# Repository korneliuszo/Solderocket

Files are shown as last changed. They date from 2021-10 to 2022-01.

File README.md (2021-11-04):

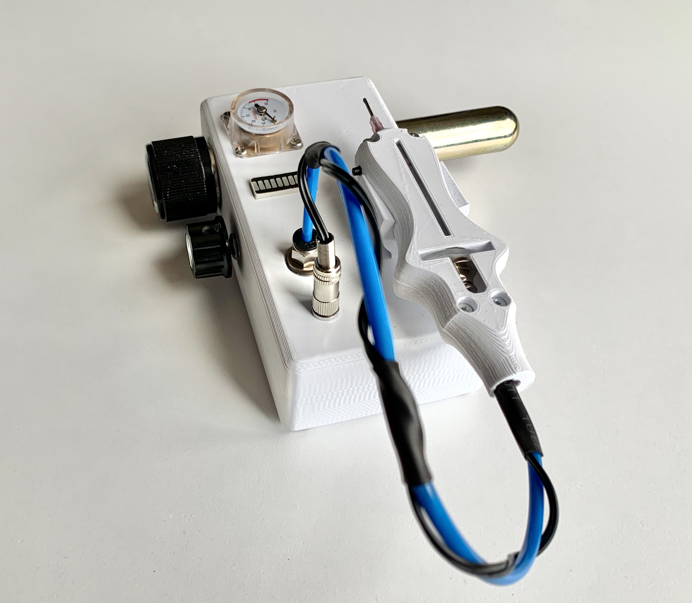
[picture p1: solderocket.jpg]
Solderocket


# Solderocket
Regular solder paste dispensers must be connected to compressed air which you can provide with huge compressor. As a maker I can not run a large compressor in my room because of its noise and footprint.

Stencils might be a solution but for small size PCB work they are too dirty and I don't like to touch the chemical solder paste with my hands and tools. It takes more time to clean up every time than apply it to the PCB.

That's why I decided to design a desktop solder paste dispenser that is clean, easy to use and small in size. I call it Solderocket.

Using the rotary knobs, the time and pressure can be set so that the right dot size can be selected for each type of solder paste.

This device is indispensable when working with SMD on a regular basis. SMD paste can be dosed very accurately and quickly. Adhesives can be used in addition to SMD paste.

# Specifications
* No Compressor needed. Works with Co2 cartridges.
* Adjustable pressure 0-60 psi 
* Adjustable timing from 50 millisecond up to trigger release.
* Ergonomic Injector hand tool
* Dimensions : 155 x 120 x 75 mm
* Weight : 770 gr  (without packaging)
* Works with 12V DC adapter

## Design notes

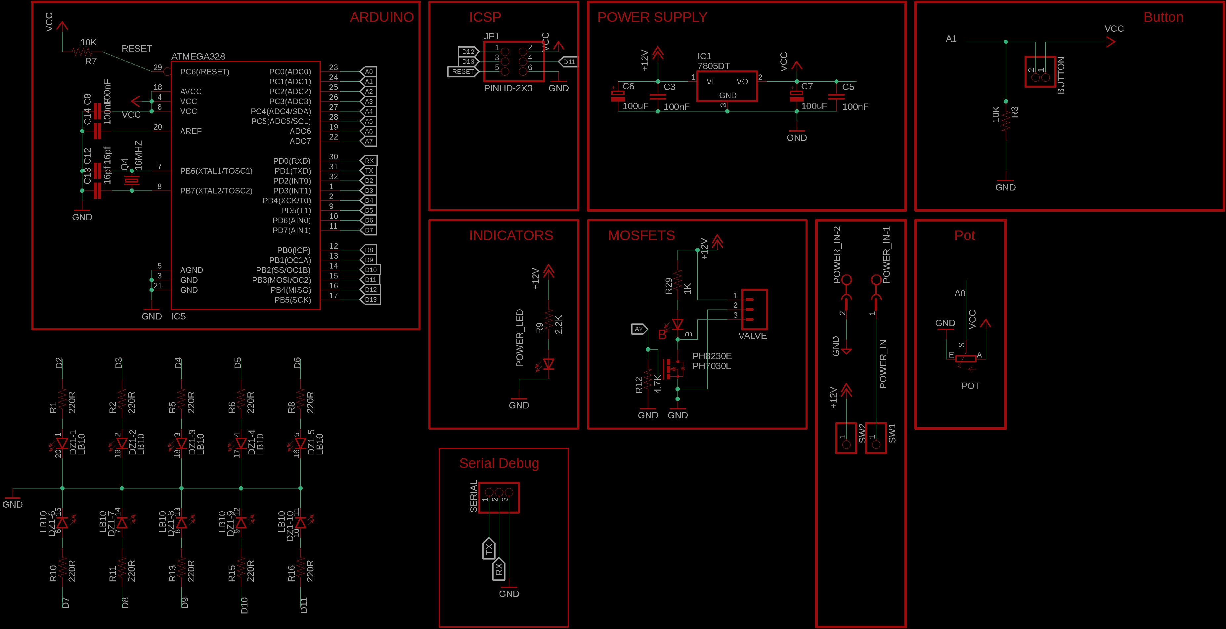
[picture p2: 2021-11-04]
pcb/schematic_img.png

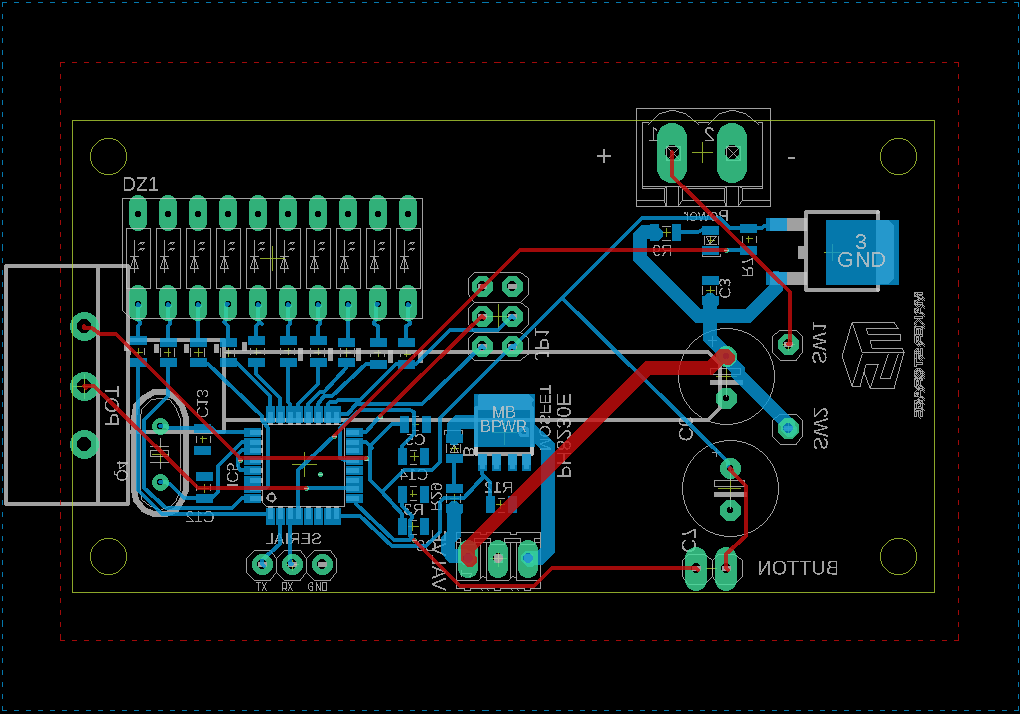
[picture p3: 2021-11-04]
pcb/board_image.png

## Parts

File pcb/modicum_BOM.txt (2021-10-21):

Partlist exported from /home/nuri/electronics/modicum/pcb/modicum.sch at 14.10.2021 13:22

Qty Value     Device             Package    Parts                                       Description                              CATEGORY  DESCRIPTION MANUFACTURER MF MPN OC_FARNELL OC_NEWARK OPERATING_TEMP PART_STATUS POPULARITY ROHS_COMPLIANT SERIES SUB-CATEGORY THERMALLOSS TYPE
2             LED0805            LED-0805   B, POWER_LED                                LEDs                                                                                                                                                                                             
1             M03                03P        VALVE                                       AMP QUICK CONNECTOR                                                                unknown    unknown                              12                                                            
2             PINHD-1X1          1X01       SW1, SW2                                    PIN HEADER                                                                                                                         64                                                            
1             PINHD-1X2          1X02       BUTTON                                      PIN HEADER                                                                                                                         98                                                            
1             PINHD-1X3          1X03       SERIAL                                      PIN HEADER                                                                                                                                                                                       
1             TRIM_EU-CIP20C-6MM CIP20C-6MM POT                                         POTENTIOMETER                                                                                                                                                                                    
4   100nF     CAP0805            0805       C3, C5, C8, C14                             Capacitor                                                                                                                                                                                        
2   100uF     CPOL-EUE3.5-8      E3,5-8     C6, C7                                      POLARIZED CAPACITOR, European symbol                                                                                                                                                             
2   10K       RESISTOR           0805       R3, R7                                      Resistor                                                                                                                                                                                         
1   16MHZ     CRYSTALHC49S       HC49/S     Q4                                          CRYSTAL                                                                                                                                                                                          
2   16pf      CAP0805            0805       C12, C13                                    Capacitor                                                                                                                                                                                        
1   1K        RESISTOR           0805       R29                                         Resistor                                                                                                                                                                                         
1   2.2K      RESISTOR           0805       R9                                          Resistor                                                                                                                                                                                         
10  220R      RESISTOR           0805       R1, R2, R5, R6, R8, R10, R11, R13, R15, R16 Resistor                                                                                                                                                                                         
1   4.7K      RESISTOR           0805       R12                                         Resistor                                                                                                                                                                                         
1   7805DT    7805DT             TO252      IC1                                         Positive VOLTAGE REGULATOR                                                                                                                                                                       
1   ATMEGA328 ATMEGA168          TQFP32-08  IC5                                                                                                                                                                                                                                          
1   LB10      LB10               LB10       DZ1                                         LED BLOCK                                                                                                                          1                                                             
1   MST2V     MST2V              MSTBV2     POWER_IN                                    PHOENIX                                                                                                                                                                                          
1   PH7030L   PH7030L            SOT669     PH8230E                                     N-channel TrenchMOS (TM) logic level FET                                                                                                                                                         
1   PINHD-2X3 PINHD-2X3          2X03       JP1                                         PIN HEADER                               CONNECTOR                                                                                                                  PIN-HEADER

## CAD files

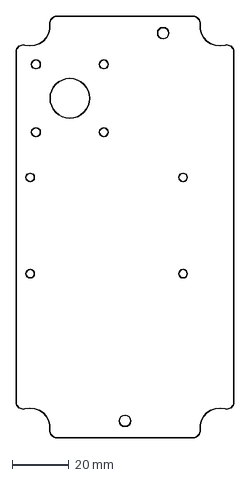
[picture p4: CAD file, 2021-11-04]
2D_Files/sheet_metal.dxf
77.0 x 149.0 mm

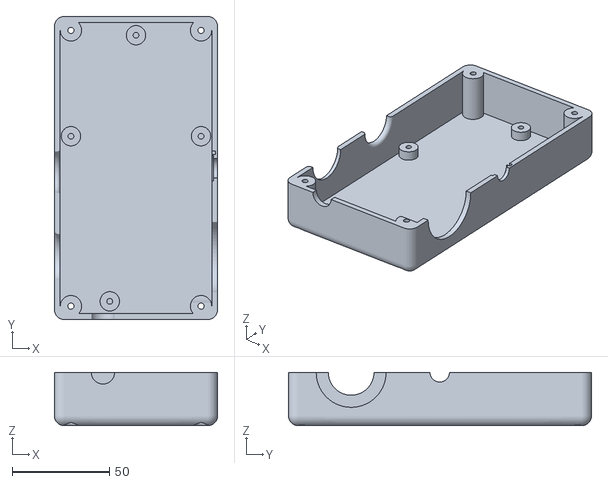
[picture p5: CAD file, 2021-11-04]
3D_files/STL/alt v70.stl
84.0 x 156.0 x 27.4

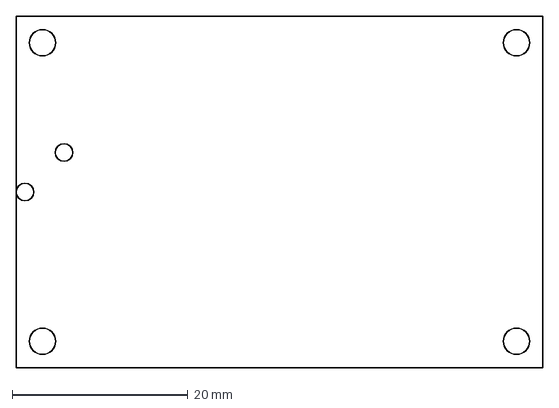
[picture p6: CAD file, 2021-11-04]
2D_Files/pcb.dxf
60.0 x 40.0 mm

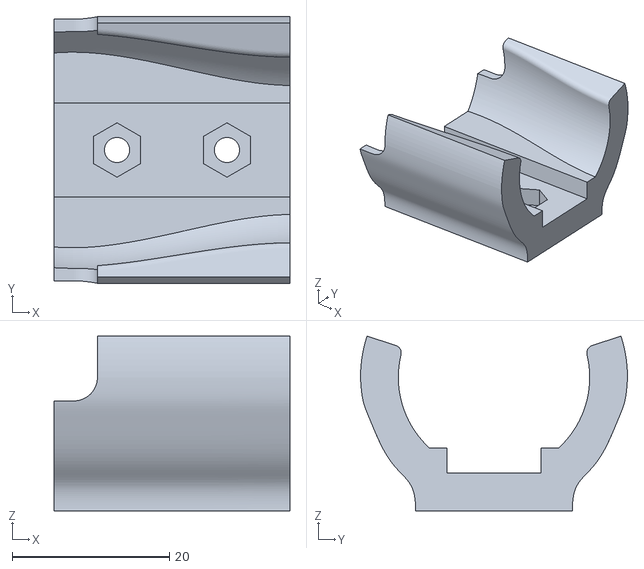
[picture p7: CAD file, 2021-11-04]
3D_files/STL/el_tutac v20.stl
30.0 x 34.0 x 22.3

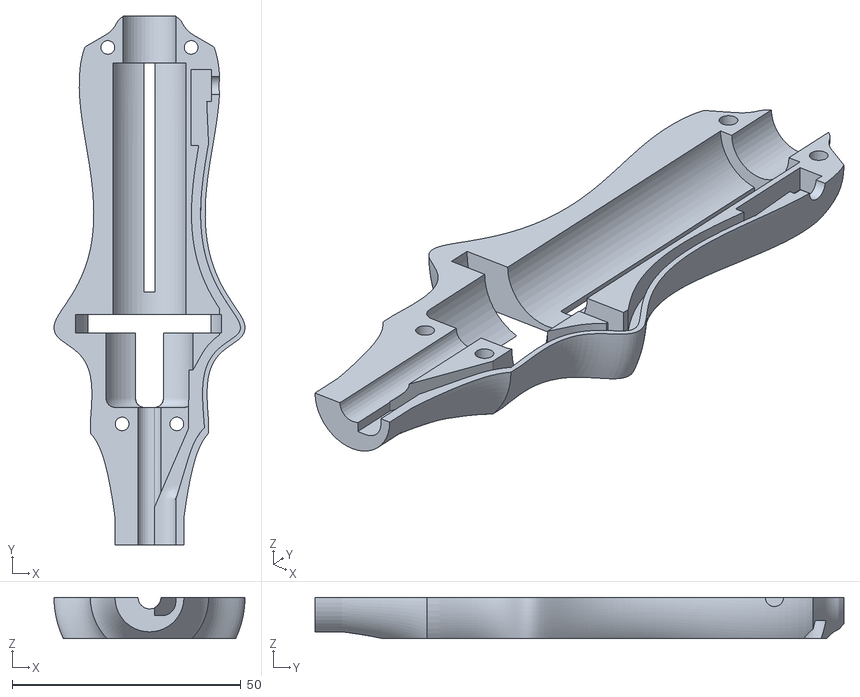
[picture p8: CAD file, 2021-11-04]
3D_files/STL/syringe_holder_alt v55.stl
41.7 x 115.5 x 9.00

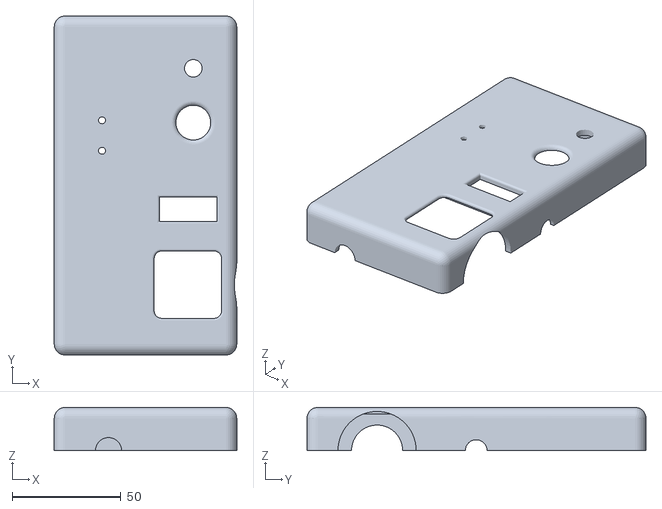
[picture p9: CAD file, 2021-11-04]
3D_files/STL/ust v64.stl
84.0 x 156.0 x 19.9

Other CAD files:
3D_files/STL/syringe_holder_ust v3.stl

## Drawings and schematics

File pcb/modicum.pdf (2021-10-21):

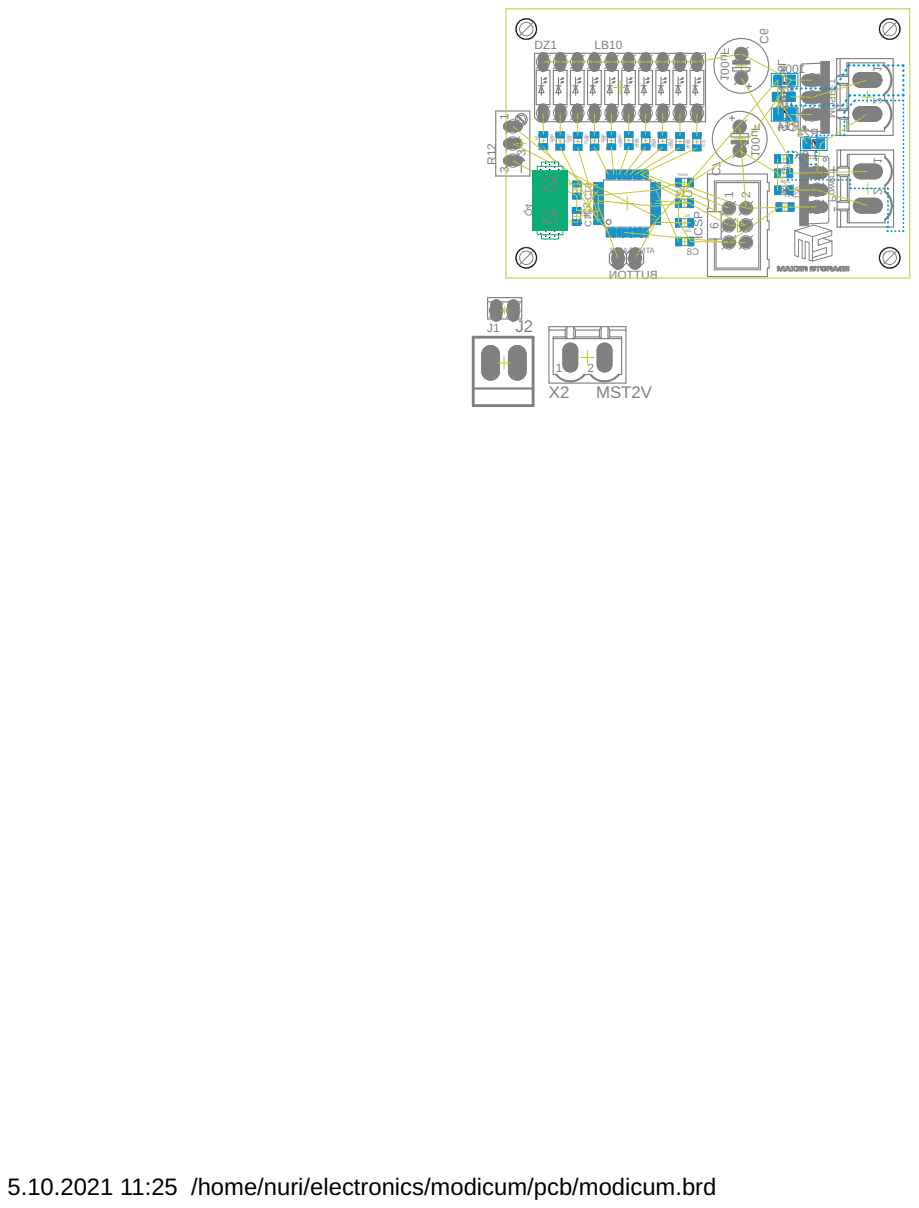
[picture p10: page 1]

5.10.2021 11:25 /home/nuri/electronics/modicum/pcb/modicum.brd

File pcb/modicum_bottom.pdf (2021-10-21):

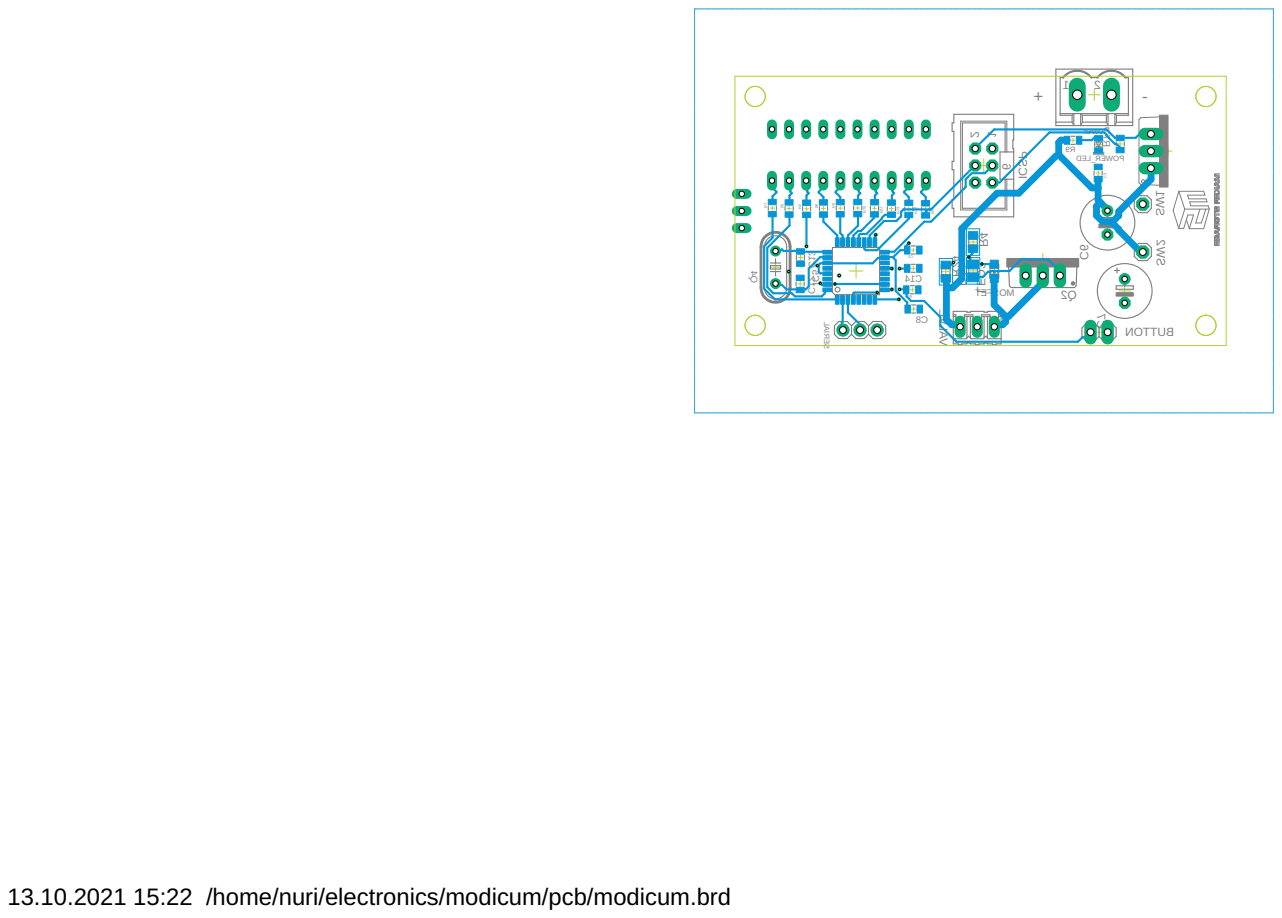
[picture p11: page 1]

13.10.2021 15:22 /home/nuri/electronics/modicum/pcb/modicum.brd

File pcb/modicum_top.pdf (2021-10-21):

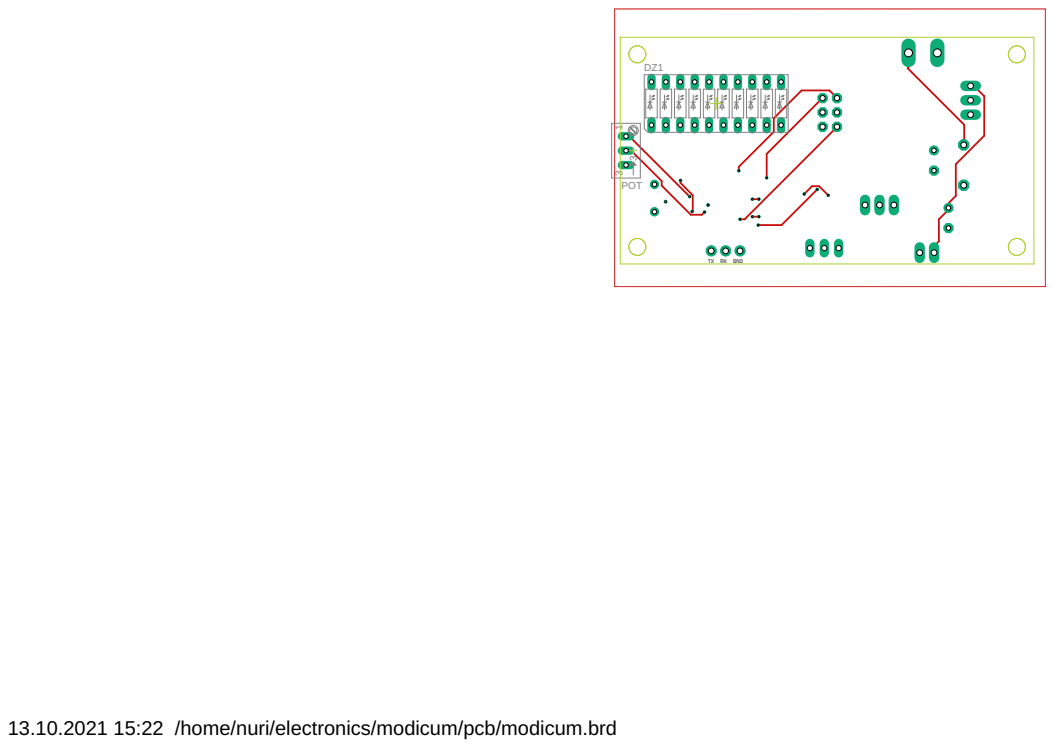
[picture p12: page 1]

13.10.2021 15:22 /home/nuri/electronics/modicum/pcb/modicum.brd

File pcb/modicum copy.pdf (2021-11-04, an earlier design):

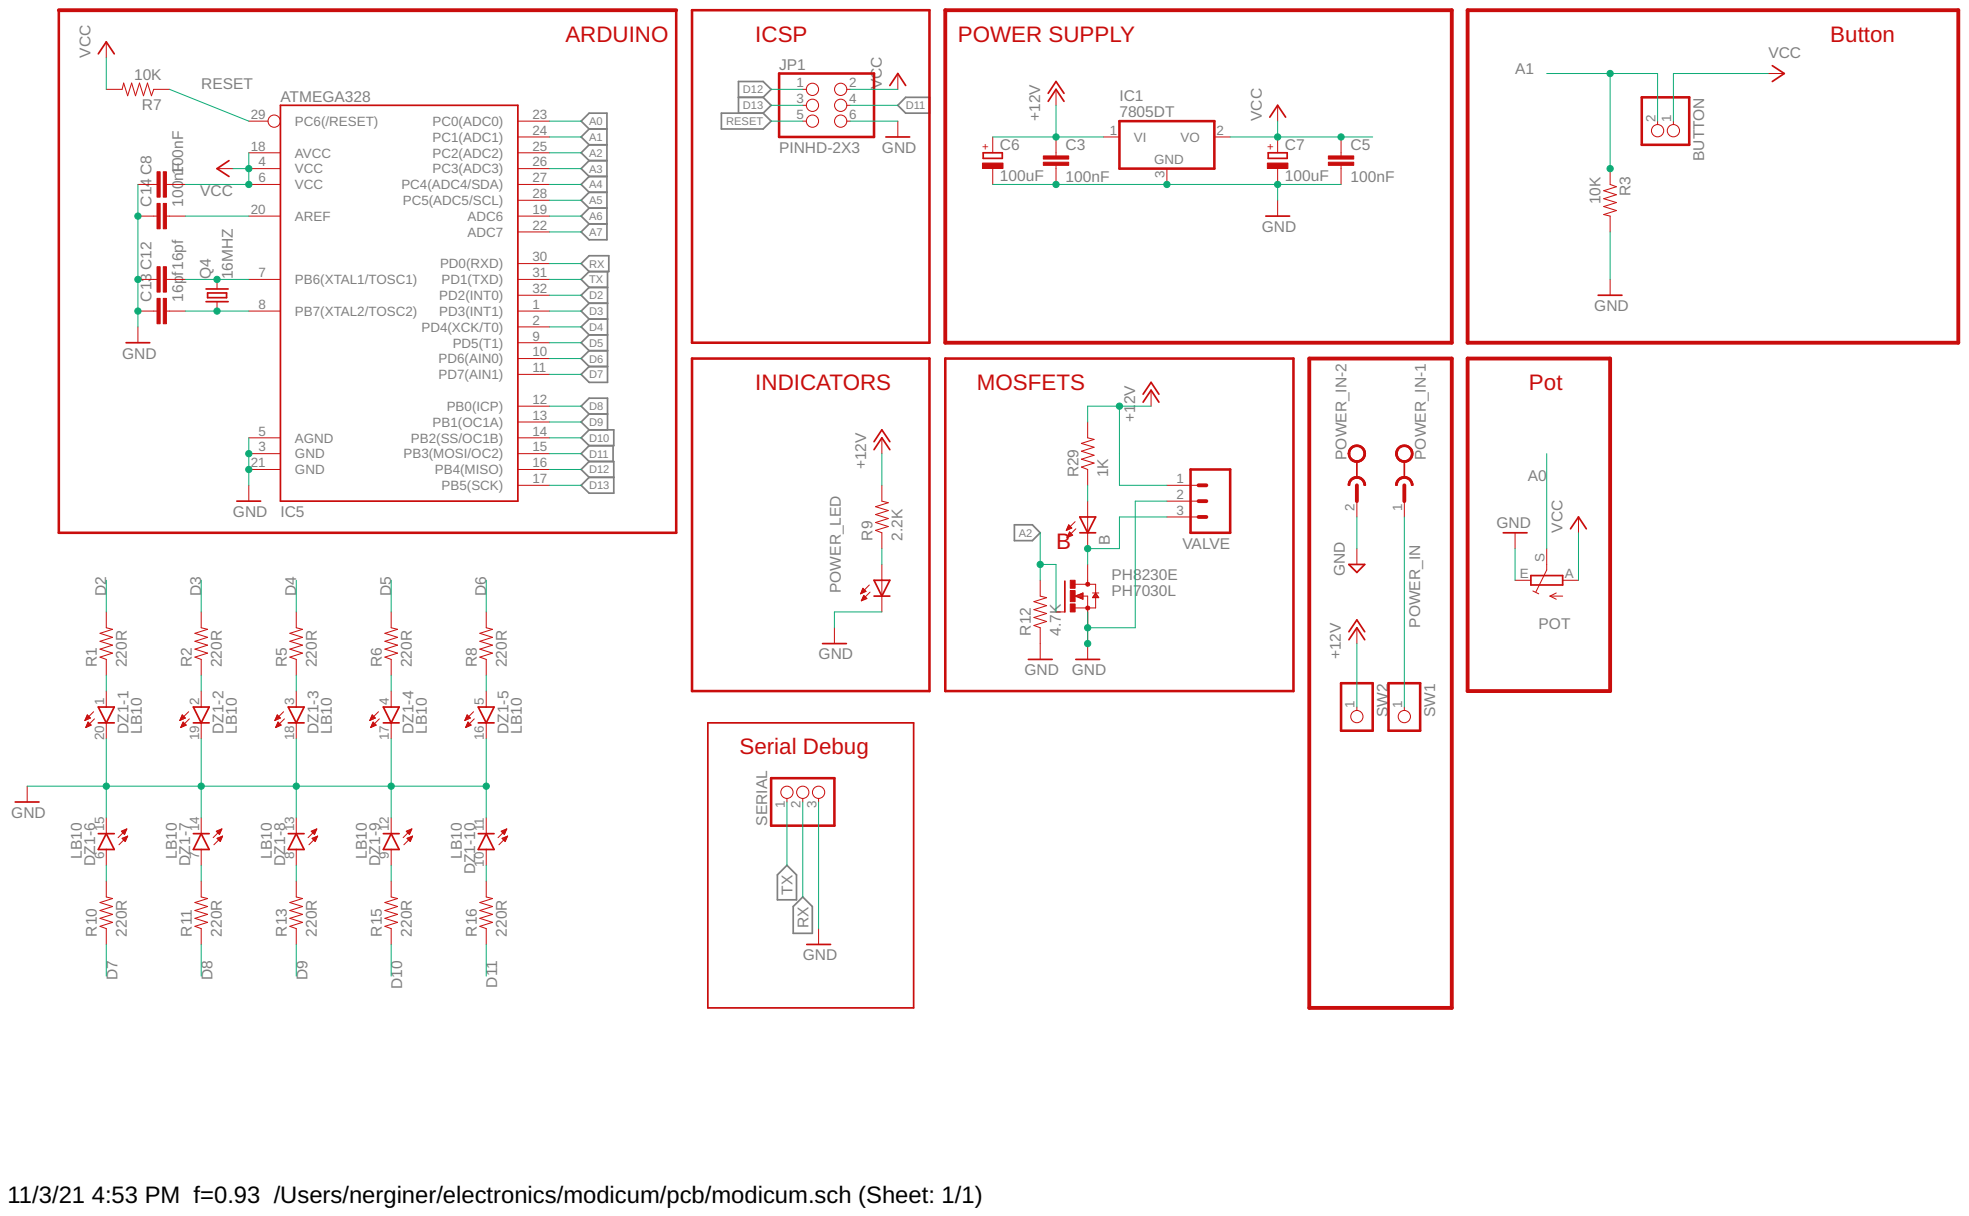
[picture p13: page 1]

11/3/21 4:53 PM f=0.93 /Users/nerginer/electronics/modicum/pcb/modicum.sch (Sheet: 1/1)

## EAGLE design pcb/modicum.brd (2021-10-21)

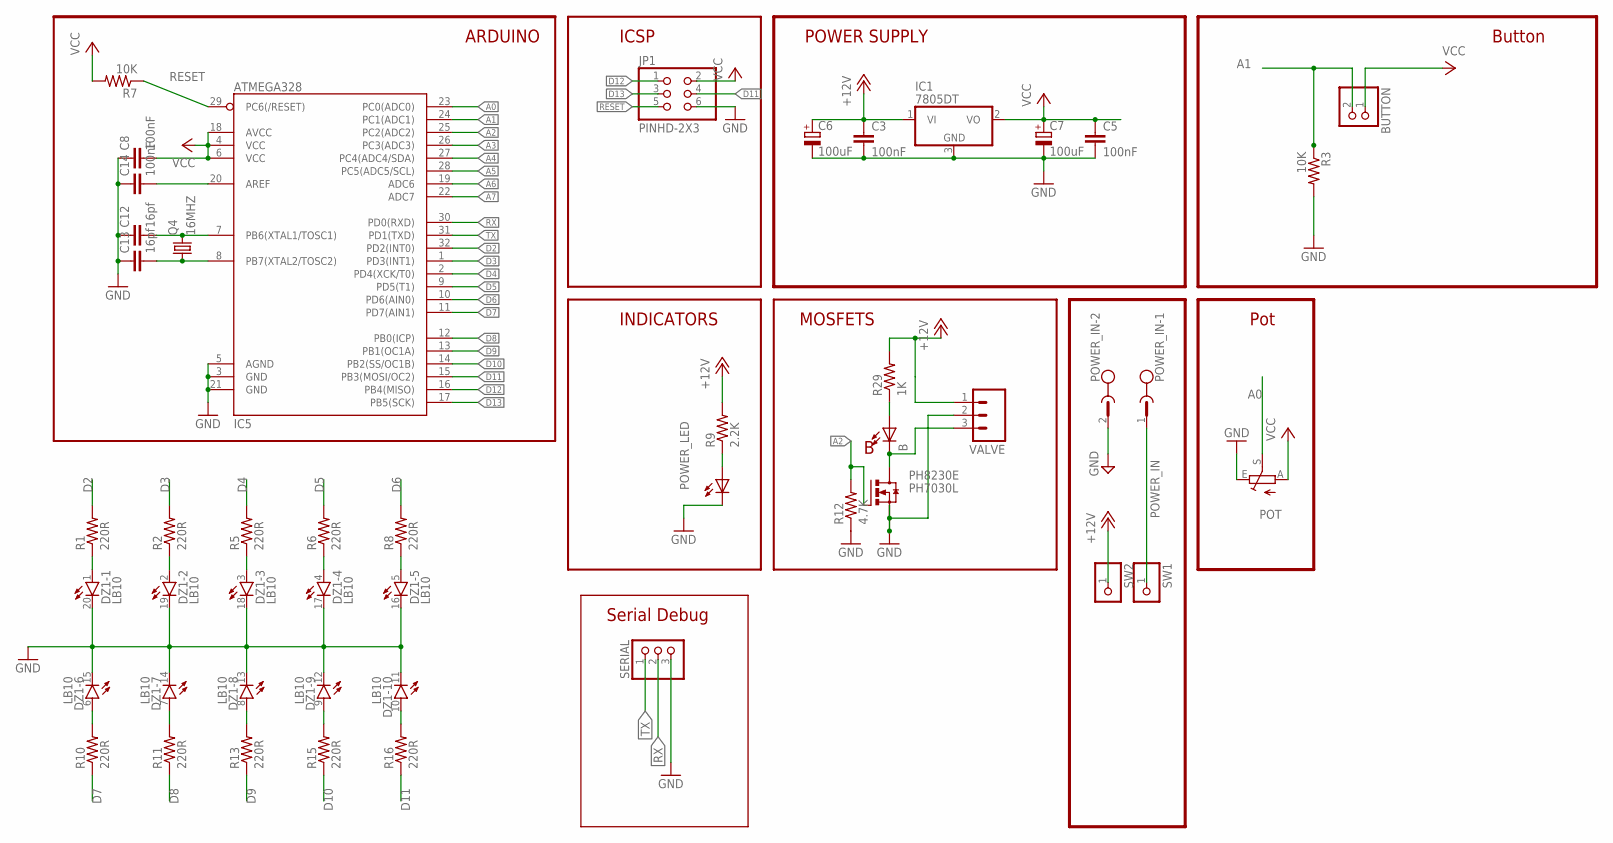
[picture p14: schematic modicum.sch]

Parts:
B: LED0805; LED-0805
BUTTON: PINHD-1X2; 1X02
C3, C5, C8, C14: 100nF; 0805
C6, C7: 100uF; E3,5-8
C12, C13: 16pf; 0805
DZ1: LB10
IC1: 7805DT; TO252
IC5: ATMEGA328; TQFP32-08
JP1: PINHD-2X3; 2X03
PH8230E: PH7030L; SOT669
POT: TRIM_EU-CIP20C-6MM; CIP20C-6MM
POWER_IN: MST2V; MSTBV2
POWER_LED: LED0805; LED-0805
Q4: 16MHZ; HC49/S
R1, R2, R5, R6, R8, R10, R11, R13, R15, R16: 220R; 0805
R3, R7: 10K; 0805
R9: 2.2K; 0805
R12: 4.7K; 0805
R29: 1K; 0805
SERIAL: PINHD-1X3; 1X03
SW1, SW2: PINHD-1X1; 1X01
VALVE: M03; 03P

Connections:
+12V: C3.1, C6.+, IC1.1 (VI), R9.2, R29.2, SW2.1, VALVE.1
A0: IC5.23 (PC0(ADC0)), POT.S
A1: BUTTON.2, IC5.24 (PC1(ADC1)), R3.1
A2: IC5.25 (PC2(ADC2)), PH8230E.4 (G), R12.2
A3: IC5.26 (PC3(ADC3))
A4: IC5.27 (PC4(ADC4/SDA))
A5: IC5.28 (PC5(ADC5/SCL))
A6: IC5.19 (ADC6)
A7: IC5.22 (ADC7)
BPWR: B.C, PH8230E.MB (D), VALVE.3
D2: IC5.32 (PD2(INT0)), R1.2
D3: IC5.1 (PD3(INT1)), R2.2
D4: IC5.2 (PD4(XCK/T0)), R5.2
D5: IC5.9 (PD5(T1)), R6.2
D6: IC5.10 (PD6(AIN0)), R8.2
D7: IC5.11 (PD7(AIN1)), R10.1
D8: IC5.12 (PB0(ICP)), R11.1
D9: IC5.13 (PB1(OC1A)), R13.1
D10: IC5.14 (PB2(SS/OC1B)), R15.1
D11: IC5.15 (PB3(MOSI/OC2)), JP1.4, R16.1
D12: IC5.16 (PB4(MISO)), JP1.1
D13: IC5.17 (PB5(SCK)), JP1.3
GND: C3.2, C5.2, C6.-, C7.-, C8.1, C12.1, C13.1, C14.1, DZ1.11 (C), DZ1.12 (C), DZ1.13 (C), DZ1.14 (C), DZ1.15 (C), DZ1.16 (C), DZ1.17 (C), DZ1.18 (C), DZ1.19 (C), DZ1.20 (C), IC1.3 (GND), IC5.3 (GND), IC5.5 (AGND), IC5.21 (GND), JP1.6, PH8230E.1 (S), PH8230E.2 (S), PH8230E.3 (S), POT.E, POWER_IN.2, POWER_LED.C, R3.2, R12.1, SERIAL.3, VALVE.2
unnamed: DZ1.1 (A), R1.1
unnamed: DZ1.2 (A), R2.1
unnamed: DZ1.3 (A), R5.1
unnamed: DZ1.4 (A), R6.1
unnamed: DZ1.5 (A), R8.1
unnamed: DZ1.6 (A), R10.2
unnamed: DZ1.7 (A), R11.2
unnamed: DZ1.8 (A), R13.2
unnamed: DZ1.9 (A), R15.2
unnamed: DZ1.10 (A), R16.2
unnamed: C14.2, IC5.20 (AREF)
unnamed: POWER_LED.A, R9.1
unnamed: C12.2, IC5.7 (PB6(XTAL1/TOSC1)), Q4.2
unnamed: C13.2, IC5.8 (PB7(XTAL2/TOSC2)), Q4.1
unnamed: B.A, R29.1
POWER_IN: POWER_IN.1, SW1.1
RESET: IC5.29 (PC6(/RESET)), JP1.5, R7.1
RX: IC5.30 (PD0(RXD)), SERIAL.2
TX: IC5.31 (PD1(TXD)), SERIAL.1
VCC: BUTTON.1, C5.1, C7.+, C8.2, IC1.2 (VO), IC5.4 (VCC), IC5.6 (VCC), IC5.18 (AVCC), JP1.2, POT.A, R7.2

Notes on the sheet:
MOSFETS
ICSP
ARDUINO
INDICATORS
POWER SUPPLY
Button
Pot
Serial Debug

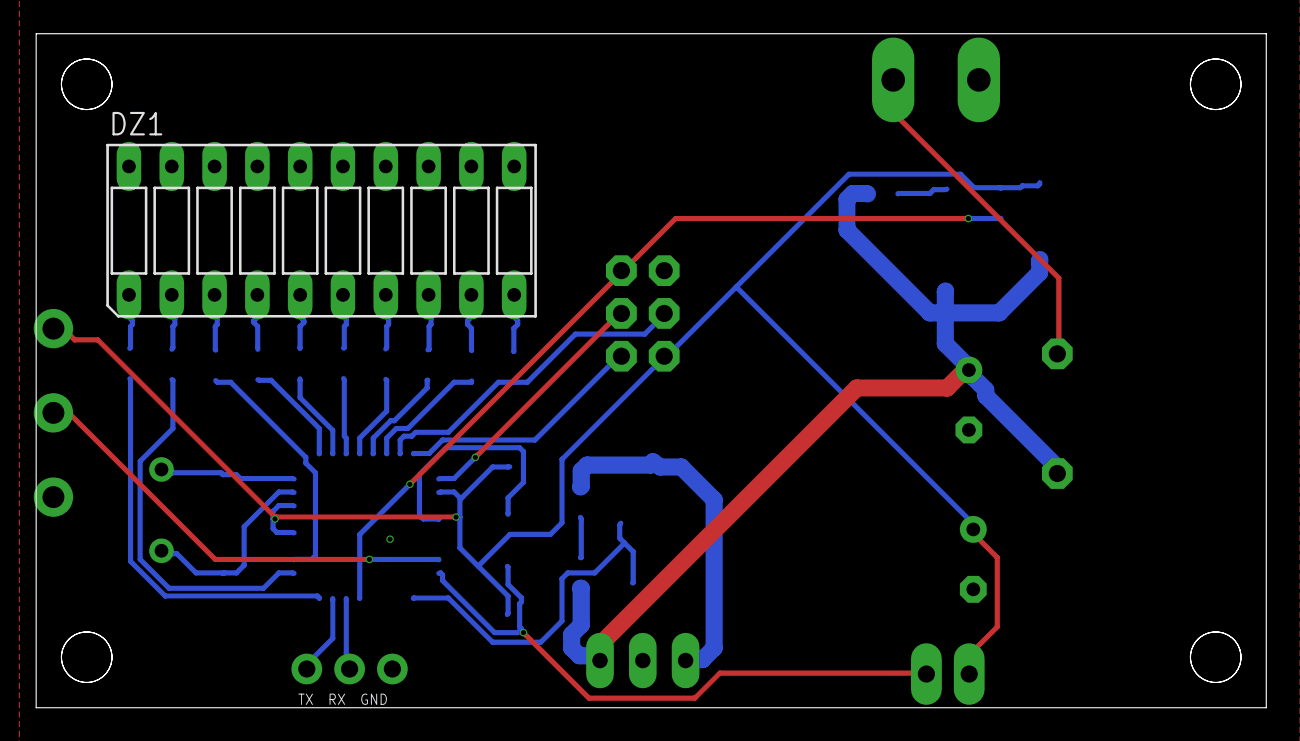
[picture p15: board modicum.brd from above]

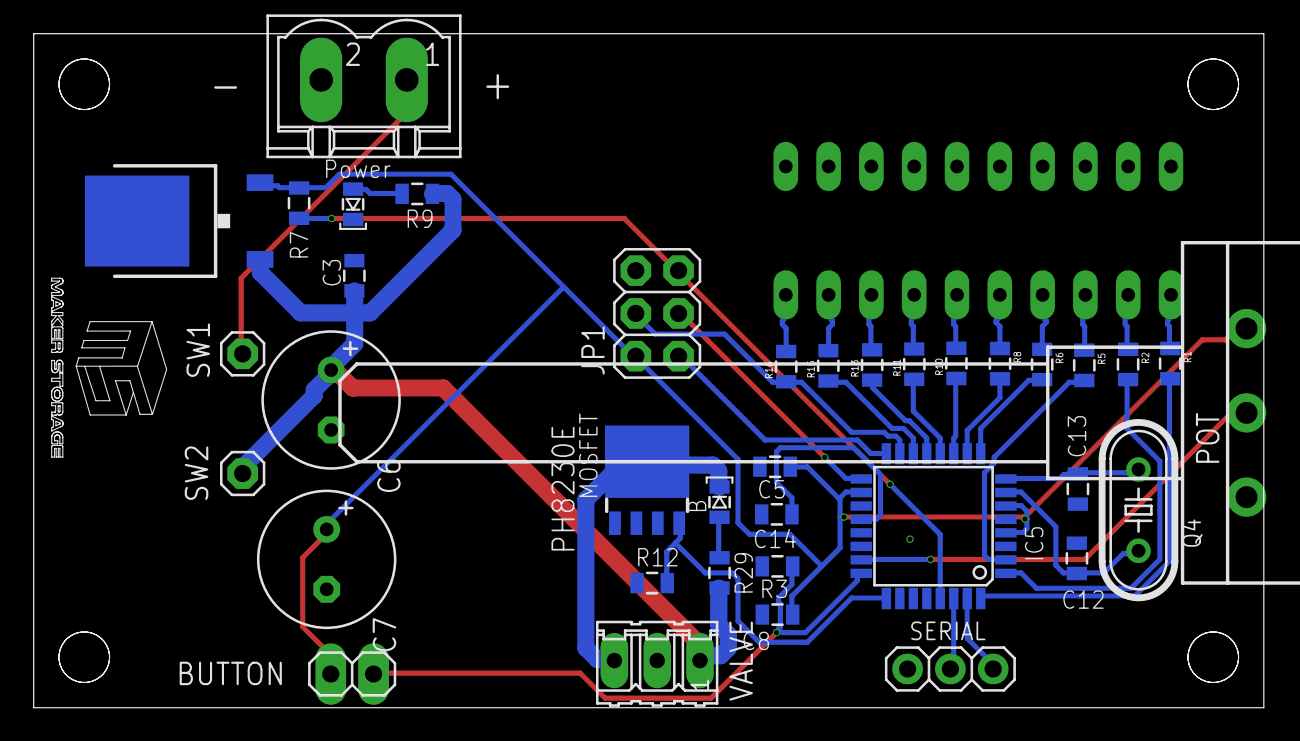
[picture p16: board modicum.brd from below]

Board: 2 copper layers, 73.0 x 40.0 mm, 38 parts (37 on the bottom side), 38 nets.

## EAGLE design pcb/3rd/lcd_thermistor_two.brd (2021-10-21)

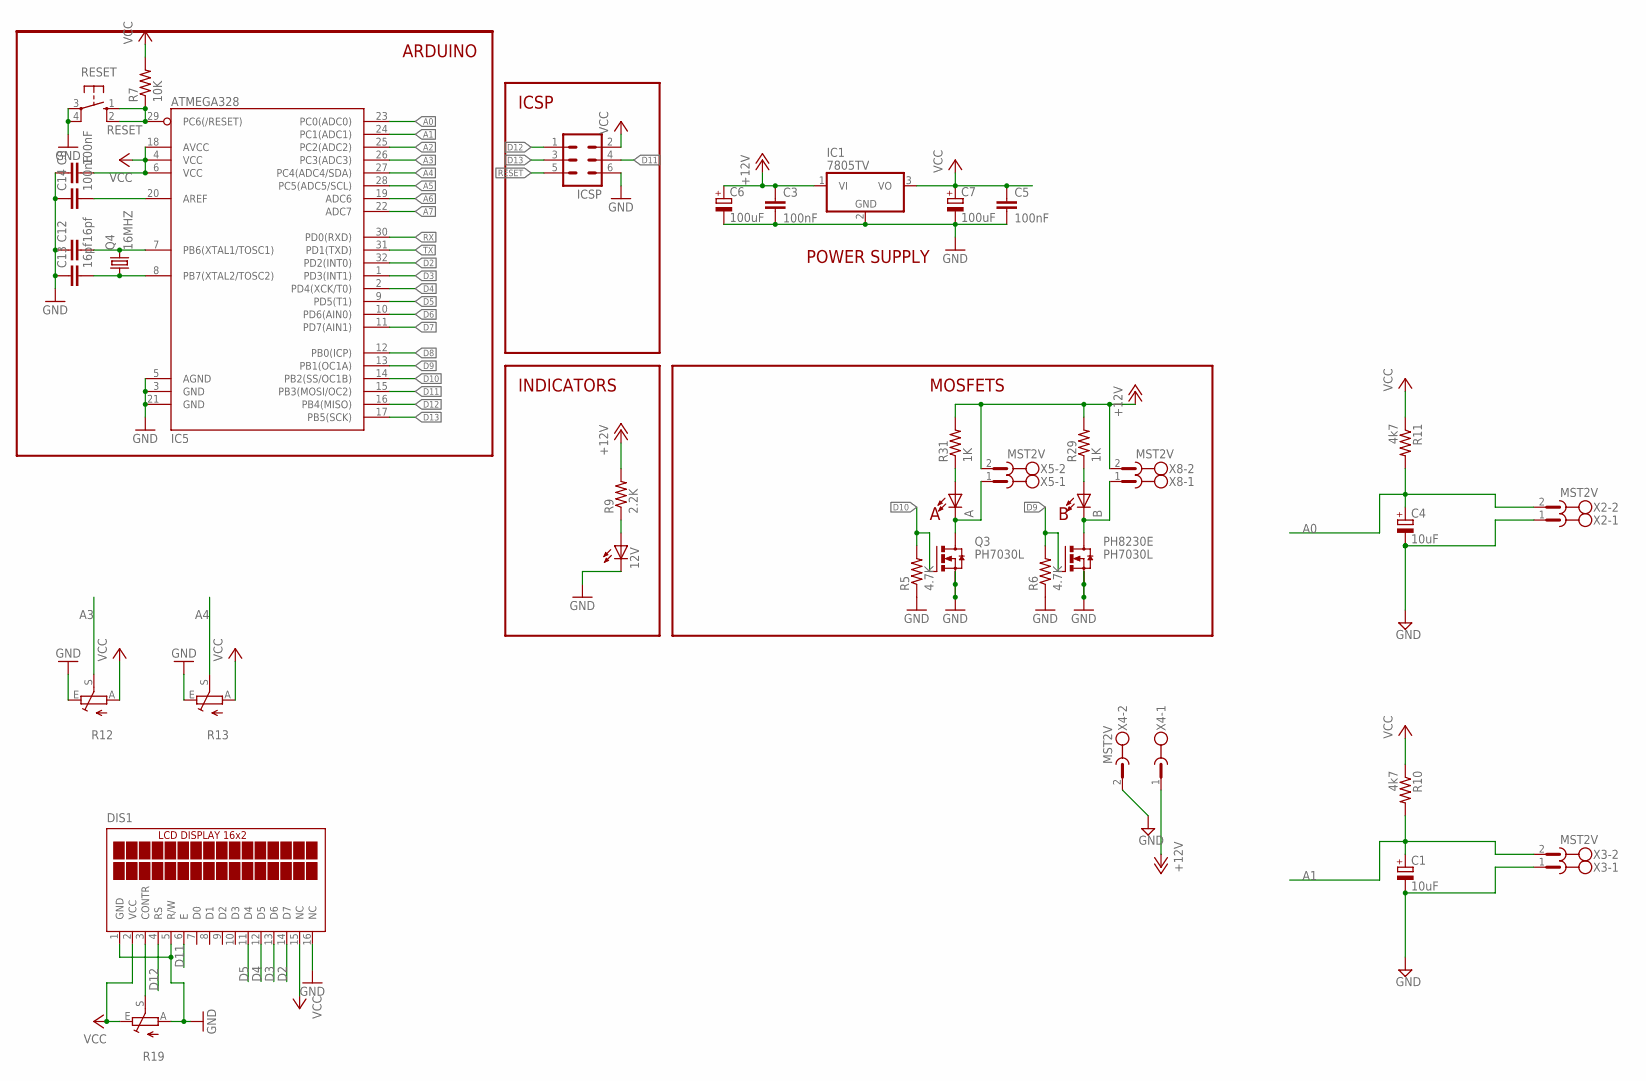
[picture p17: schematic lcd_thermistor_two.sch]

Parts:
12V: LED0805; LED-0805
A: LED0805; LED-0805
B: LED0805; LED-0805
C1, C4: 10uF; E5-6
C3, C5, C8, C14: 100nF; 0805
C6, C7: 100uF; E3,5-8
C12, C13: 16pf; 0805
DIS1: TUXGR_16X2_R2
IC1: 7805TV; TO220V
IC5: ATMEGA328; TQFP32-08
ICSP: ML6
PH8230E: PH7030L; SOT669
Q3: PH7030L; SOT669
Q4: 16MHZ; HC49/S
R5, R6: 4.7K; 0805
R7: 10K; 0805
R9: 2.2K; 0805
R10, R11: 4k7; 0805
R12, R13: TRIM_EU-B25U; B25U
R19: TRIM_EU-B25P; B25P
R29, R31: 1K; 0805
RESET: 10-XX; B3F-10XX
X2, X3, X4, X5, X8: MST2V; MSTBV2

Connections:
+12V: C3.1, C6.+, IC1.1 (VI), R9.2, R29.2, R31.2, X4.1, X5.2, X8.2
A0: C4.+, IC5.23 (PC0(ADC0)), R11.2, X2.2
A1: C1.+, IC5.24 (PC1(ADC1)), R10.2, X3.2
A2: IC5.25 (PC2(ADC2))
A3: IC5.26 (PC3(ADC3)), R12.S
A4: IC5.27 (PC4(ADC4/SDA)), R13.S
A5: IC5.28 (PC5(ADC5/SCL))
A6: IC5.19 (ADC6)
A7: IC5.22 (ADC7)
APWR: A.C, Q3.MB (D), X5.1
BPWR: B.C, PH8230E.MB (D), X8.1
D2: DIS1.14 (D7), IC5.32 (PD2(INT0))
D3: DIS1.13 (D6), IC5.1 (PD3(INT1))
D4: DIS1.12 (D5), IC5.2 (PD4(XCK/T0))
D5: DIS1.11 (D4), IC5.9 (PD5(T1))
D6: IC5.10 (PD6(AIN0))
D7: IC5.11 (PD7(AIN1))
D8: IC5.12 (PB0(ICP))
D9: IC5.13 (PB1(OC1A)), PH8230E.4 (G), R6.2
D10: IC5.14 (PB2(SS/OC1B)), Q3.4 (G), R5.2
D11: DIS1.6 (E), IC5.15 (PB3(MOSI/OC2)), ICSP.4
D12: DIS1.4 (RS), IC5.16 (PB4(MISO)), ICSP.1
D13: IC5.17 (PB5(SCK)), ICSP.3
GND: 12V.C, C1.-, C3.2, C4.-, C5.2, C6.-, C7.-, C8.1, C12.1, C13.1, C14.1, DIS1.1 (GND), DIS1.5 (R/W), DIS1.16 (NC), IC1.2 (GND), IC5.3 (GND), IC5.5 (AGND), IC5.21 (GND), ICSP.6, PH8230E.1 (S), PH8230E.2 (S), PH8230E.3 (S), Q3.1 (S), Q3.2 (S), Q3.3 (S), R5.1, R6.1, R12.E, R13.E, R19.A, RESET.3, RESET.4 (P1), X2.1, X3.1, X4.2
unnamed: C14.2, IC5.20 (AREF)
unnamed: 12V.A, R9.1
unnamed: DIS1.3 (CONTR), R19.S
unnamed: C12.2, IC5.7 (PB6(XTAL1/TOSC1)), Q4.2
unnamed: C13.2, IC5.8 (PB7(XTAL2/TOSC2)), Q4.1
unnamed: A.A, R31.1
unnamed: B.A, R29.1
RESET: IC5.29 (PC6(/RESET)), ICSP.5, R7.1, RESET.1 (S), RESET.2 (S1)
RX: IC5.30 (PD0(RXD))
TX: IC5.31 (PD1(TXD))
VCC: C5.1, C7.+, C8.2, DIS1.2 (VCC), DIS1.15 (NC), IC1.3 (VO), IC5.4 (VCC), IC5.6 (VCC), IC5.18 (AVCC), ICSP.2, R7.2, R10.1, R11.1, R12.A, R13.A, R19.E

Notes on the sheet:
MOSFETS
ICSP
ARDUINO
INDICATORS
POWER SUPPLY

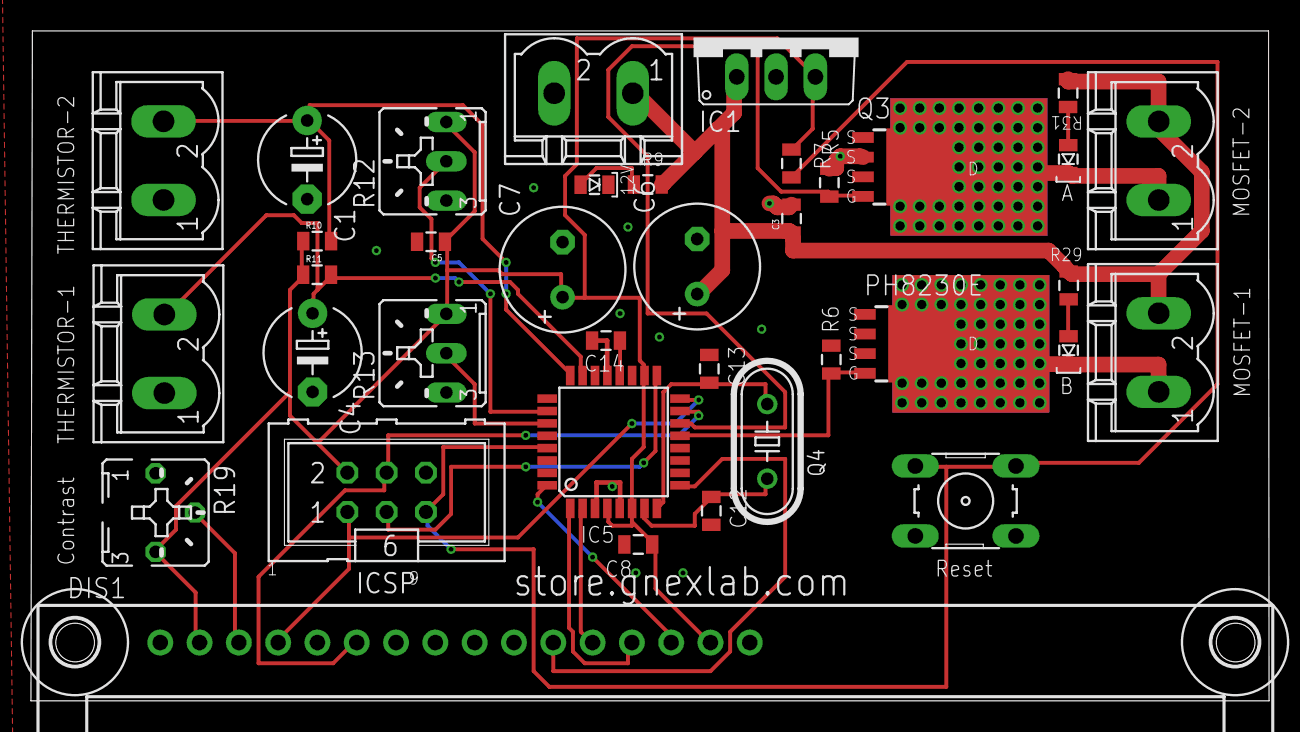
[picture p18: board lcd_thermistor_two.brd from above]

Board: 2 copper layers, 80.0 x 43.3 mm, 39 parts (0 on the bottom side), 26 nets.

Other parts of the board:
U$1, U$4: 3,0

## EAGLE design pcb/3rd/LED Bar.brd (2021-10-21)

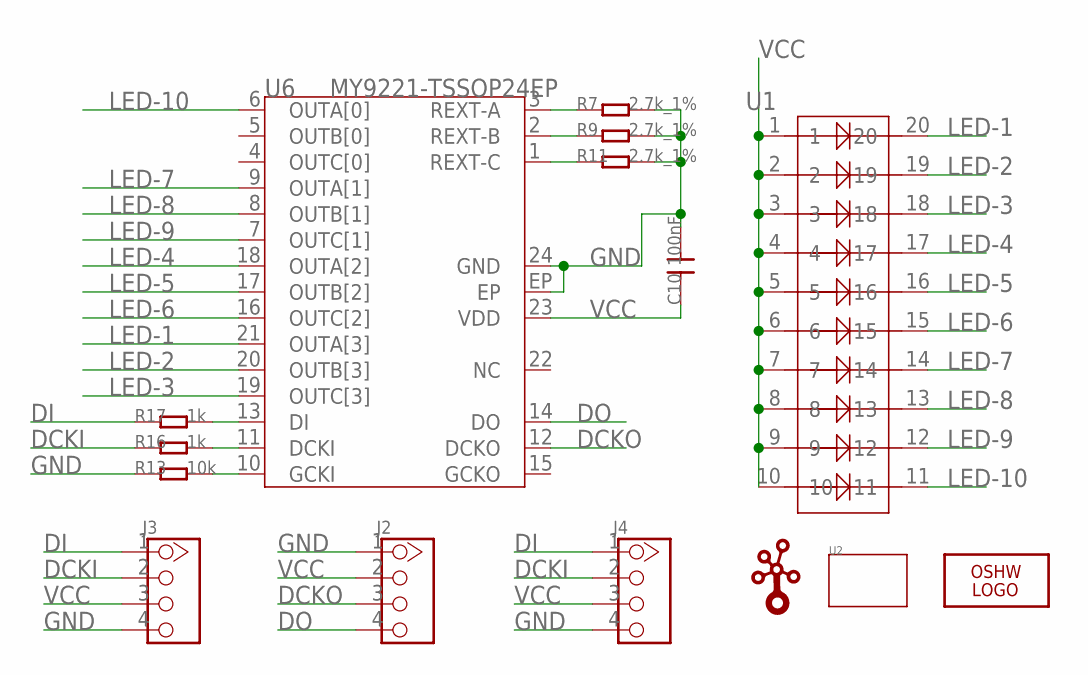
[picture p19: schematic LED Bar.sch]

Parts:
C10: 100nF; 0603
J2: HEADER-4P-90D; 4P-2.54-90
J3: HEADER-4P'2.54-90D-FEMALE'; 4P-2.54-90D-FEMALE
J4: TWIG-4P-2.0-2.0; 4P-2.0
LOGO1: LOGO-OSHW-FILLX0150-NT; OSHW_FILLX150_NOTEXT
R7, R9, R11: 2.7k_1%; 0603
R13: 10k; 0603
R16, R17: 1k; 0603
U1: LED-20P; 20P-DIP-2.54-25.5X10.1X8.4H
U2: TWIG-2U; 2U-DIM-W/-DRILL
U6: MY9221-TSSOP24EP; TSSOP24EP
U$1: LOGO-TWIGTWIGLOGO_SMALL; TWIGLOGO_SMALL

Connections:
DCKI: J3.2, J4.2, R16.1
DCKO: J2.3, U6.12 (DCKO)
DI: J3.1, J4.1, R17.1
DO: J2.4, U6.14 (DO)
GND: C10.2, J2.1, J3.4, J4.4, R7.2, R9.2, R11.2, R13.1, U6.24 (GND), U6.EP
LED-1: U1.20, U6.21 (OUTA[3])
LED-2: U1.19, U6.20 (OUTB[3])
LED-3: U1.18, U6.19 (OUTC[3])
LED-4: U1.17, U6.18 (OUTA[2])
LED-5: U1.16, U6.17 (OUTB[2])
LED-6: U1.15, U6.16 (OUTC[2])
LED-7: U1.14, U6.9 (OUTA[1])
LED-8: U1.13, U6.8 (OUTB[1])
LED-9: U1.12, U6.7 (OUTC[1])
LED-10: U1.11, U6.6 (OUTA[0])
unnamed: R17.2, U6.13 (DI)
unnamed: R16.2, U6.11 (DCKI)
unnamed: R13.2, U6.10 (GCKI)
unnamed: R11.1, U6.1 (REXT-C)
unnamed: R9.1, U6.2 (REXT-B)
unnamed: R7.1, U6.3 (REXT-A)
VCC: C10.1, J2.2, J3.3, J4.3, U1.1, U1.2, U1.3, U1.4, U1.5, U1.6, U1.7, U1.8, U1.9, U1.10, U6.23 (VDD)

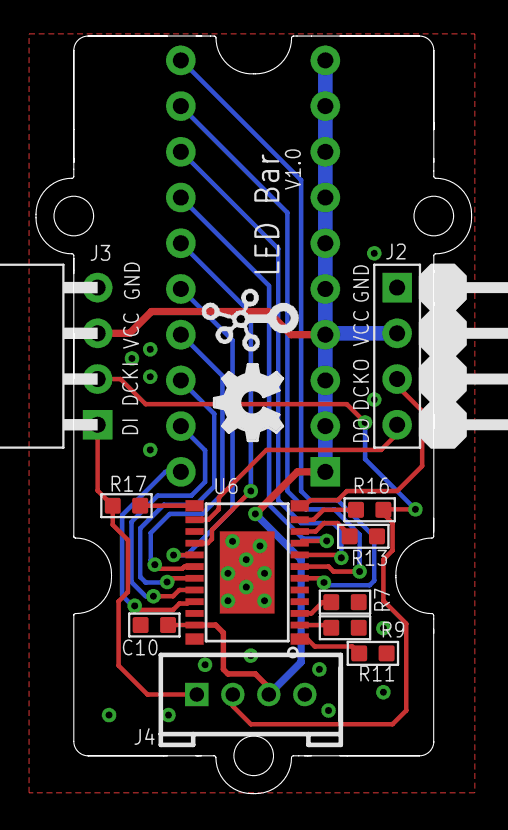
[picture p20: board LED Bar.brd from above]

Board: 2 copper layers, 24.2 x 42.1 mm, 15 parts (1 on the bottom side), 22 nets.

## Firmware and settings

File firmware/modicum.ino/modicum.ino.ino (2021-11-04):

int buttonPin = 15;
int potPin = 0;
int mosfetPin = 16;
int potVal = 0;

const int numReadings = 10;
int readings[numReadings];      // the readings from the analog input
int readIndex = 0;              // the index of the current reading
int total = 0;                  // the running total
int average = 0;                // the average

int buttonState = 1;         // current state of the button, HIGH as we have active low with INPUT_PULLUP
int lastButtonState = 1;     // previous state of the button

const int ledCount = 10;    // the number of LEDs in the bar graph
int ledPins[] = {
  2, 3, 4, 5, 6, 7, 8, 9, 10, 11
};   

void setup() {
  
  // loop over the pin array and set them all to output:
  for (int thisLed = 0; thisLed < ledCount; thisLed++) {
    pinMode(ledPins[thisLed], OUTPUT);
  }
  
  pinMode(mosfetPin, OUTPUT);  
  pinMode(buttonPin, INPUT);    
  pinMode(potPin, INPUT);  

  pinMode(2, OUTPUT); // Do not know why it did not set in the above for loop

}

void loop() {

  buttonState = digitalRead(buttonPin);
    // compare the buttonState to its previous state
    if (buttonState != lastButtonState) {
  
      if (buttonState == LOW) {  
        // wend from off to on:
          digitalWrite(mosfetPin, LOW);
       
      } else {
        // if the current state is LOW then the button
        // wend from on to off:

        digitalWrite(mosfetPin, HIGH); // sets the digital pin 13 on
        delay(average);            // waits for a second
        // if in full throtle do not make it of
        if (average < 999) {
          digitalWrite(mosfetPin, LOW);
        }
          
       
      }
      // Delay a little bit to avoid bouncing
      delay(50);
    }
    // save the current state as the last state,
    //for next time through the loop
    lastButtonState = buttonState;

  average = readPot();

  showLeds(average,50,1000);
 
}

int readPot() {
  
  return map(analogRead(potPin), 0, 1023, 50, 1000);
  
}

void showLeds(int avarage,int mymin,int mymax){

  int ledLevel = map(avarage, mymin, mymax, 0, ledCount);

  // loop over the LED array:
  for (int thisLed = 0; thisLed < ledCount; thisLed++) {
    // if the array element's index is less than ledLevel,
    // turn the pin for this element on:
    if (thisLed < ledLevel) {
      digitalWrite(ledPins[thisLed], HIGH);
    }
    // turn off all pins higher than the ledLevel:
    else {
      digitalWrite(ledPins[thisLed], LOW);
    }
  }
  
}

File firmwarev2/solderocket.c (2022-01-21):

#include <stdint.h>
#include <avr/io.h>
#include <util/delay.h>

static void InitADC(void)
{
 // Select Vref=AVcc
 ADMUX = (1<<REFS0);
 //set prescaller to 128 and enable ADC 
 ADCSRA |= (1<<ADPS2)|(1<<ADPS1)|(1<<ADPS0)|(1<<ADEN);    
}

uint16_t ReadADC(uint8_t ADCchannel)
{
 //select ADC channel with safety mask
 ADMUX = (ADMUX & 0xF0) | (ADCchannel & 0x0F);
 //single conversion mode
 ADCSRA |= (1<<ADSC);
 // wait until ADC conversion is complete
 while( ADCSRA & (1<<ADSC) );
 return ADC;
}

struct {
	volatile uint8_t * port;
	uint8_t mask;
} LEDS[10] =
{
	{&PORTD,0x04},
	{&PORTD,0x08},
	{&PORTD,0x10},
	{&PORTD,0x20},
	{&PORTD,0x40},
	{&PORTD,0x80},
	{&PORTB,0x01},
	{&PORTB,0x02},
	{&PORTB,0x04},
	{&PORTB,0x08},
};

typedef struct {
	uint16_t delay;
	uint16_t led;
} Delays;

//[ round(50*math.exp(x)) for x in [math.log(1000/50)*x/18 for x in range(19)]]

Delays delays[]=
{
	{  50, 0b0000000001},
	{  59, 0b0000000011},
	{  70, 0b0000000010},
	{  82, 0b0000000110},
	{  97, 0b0000000100},
	{ 115, 0b0000001100},
	{ 136, 0b0000001000},
	{ 160, 0b0000011000},
	{ 189, 0b0000010000},
	{ 224, 0b0000110000},
	{ 264, 0b0000100000},
	{ 312, 0b0001100000},
	{ 368, 0b0001000000},
	{ 435, 0b0011000000},
	{ 514, 0b0010000000},
	{ 607, 0b0110000000},
	{ 717, 0b0100000000},
	{ 847, 0b1100000000},
	{1000, 0b1000000000},
};

#define DELAYS_LEN 19

int main(void)
{
	InitADC();
	DDRC=0x04;
	PORTC=0x00;
	DDRD=0xFF;
	PORTD=0x00;
	DDRB=0xFF;
	PORTB=0x00;
	DIDR0=0x01;
	uint8_t lastbutton = 0;	
	while(1)
	{
		uint8_t setting;
		setting = ReadADC(0)/((uint16_t)(1024.0/(DELAYS_LEN)));
		if (setting >= (DELAYS_LEN))
			setting=(DELAYS_LEN);

		uint8_t currbutton;
		currbutton = PINC&0x02;
		if (lastbutton != currbutton)
		{
			if (!currbutton)
				PORTC&=~(1<<2);
			else
			{
				PORTC|=(1<<2);
				if(setting < DELAYS_LEN)
				{
					uint16_t delay=delays[setting].delay; //don't reread
					for(uint16_t count=delay;count;count--)
						_delay_ms(1); // needs compile time value
					PORTC&=~(1<<2);
				}
			};
			lastbutton = currbutton;
			_delay_ms(50);
		};
		
		for(uint8_t led=0;led<10;led++)
			if((setting == (DELAYS_LEN)) ? 1 : (delays[setting].led & (1<<led)))
				*LEDS[led].port|=LEDS[led].mask;
			else
				*LEDS[led].port&=~LEDS[led].mask;
	};
}

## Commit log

2021-11-04 3D Files
    [alt v70.stl, el_tutac v20.stl, pcb.dxf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]
2021-11-23 Disable digital input on ADC input
